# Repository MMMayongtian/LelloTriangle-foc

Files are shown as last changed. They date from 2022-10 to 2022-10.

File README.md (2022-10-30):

# 自平衡莱洛三角形可充电版

### 介绍
**在B站[“基于LQR控制器的自平衡莱洛三角形”](https://www.bilibili.com/video/BV19v411n7mN) 基础上添加了充电模块**
主控芯片使用ESP32，并配置了调参上位机，可以很方便的通过wifi无线调参。无刷控制使用灯哥开源FOC。制作出一个方便复刻的自平衡莱洛三角形，在桌面上作为一个摆件还是非常不错的
[展示视频](https://www.bilibili.com/video/BV1b3411x7za)

<center>V1(图一)</center>

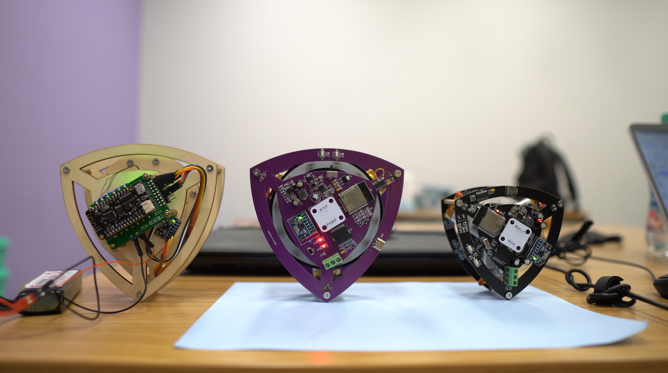
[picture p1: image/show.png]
V1


<center>V2(图二)</center>

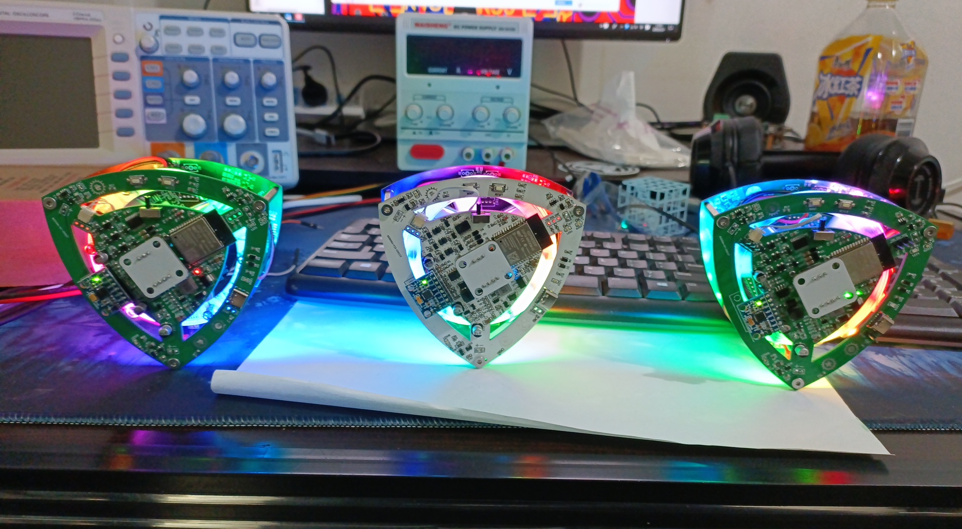
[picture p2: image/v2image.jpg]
V2


目前有两个版本
- V1(图1)：ESP32主控+L6234驱动+GB2204电机+CH340串口芯片+CS5095充电芯片
- V2(图2)：ESP32主控+EG2133+6mos驱动+2715电机+RGB+CM1010-A均衡芯片+CN3300充电芯片

**推荐制作V2，成功率高，效果更好，电机驱动芯片更便宜，还有RGB**

V1和V2**`电路图以及代码`**均在对应`V1\V2`文件夹(如需制作只要打开对应版本的文件夹即可，里面有对应的README说明)

### 1 软件架构
自平衡控制为LQR算法输出期望**速度**，使动量轮**加速运动**从而控制三角形左右方向。并且代码的调参都可以通过连接ESP32的wifi调整。具体特性如下：

- **基于 Arduino**：运行在 ESP32 Arduino 上
- **自带测试模式**：电压测试和速度测试，可以单独输出电压让电机转动，也可以设置指定速度让电机保持速度

Image text
### 2 硬件特性

| 说明 | 参数 |
| --- |--- |
| 莱洛三角形尺寸 | 100*100 mm  |
|动量轮尺寸|80*80 mm|
| 输入电压 | 3.7v锂电池*3|
|充电电压| 5V 从Type-C口输入|
| 主控芯片 | ESP-WROOM-32 |
|电机驱动|引脚:32, 33, 25|
|  AS5600 编码器 |SDA-23 SCL-5 　芯片要离径向磁铁有<font color='red'> 2mm以上高度 </font>|
| MPU6050六轴传感器  | SDA-19 SCL-18 |

### 3 硬件设计
使用立创EDA绘制电路原理图，LaserMaker绘制莱洛三角形和动量轮（有激光切割机可以事先切割结构作为参考）。将绘制完的图形导入到立创EDA中可作为PCB的外框。丝印图案分别是**Gawr Gura**、**ouro kronii** ~~helicopter~~

LaserMaker绘制的plt在**莱洛三角结构**文件夹内，需要重新绘制电路图可以使用

感谢嘉立创的PCB制板，使DIY电路制作变得非常便利，PCB制作开源点击

### 4 Ctrl+C +V（参考）
Arduino上的控制算法是原作者的LQR，无刷电机控制是灯哥开源FOC。电机控制引脚定义与传感器定义和灯哥开源FOC控制板2.0版一样。

EG2133无刷驱动为立创开源方案。

Python的GUI是以SimpleFOC的SimpleFOCStudio为基础，添加wifi功能。

V1的充电电路是立创广场开源的CS5095充电方案。

V2的充电电路是在立创广场开源的《CN3300 4串电池组板》方案基础上改的3串锂电池

PCB以及原理图技术支持——muyan

wifi效果以及按键面修复代码作者——muyan

1. 原作者：基于LQR控制器的自平衡莱洛三角形[BV19v411n7mN](https://www.bilibili.com/video/BV19v411n7mN)
2. muyan 立创链接[https://oshwhub.com/muyan2020?tab=project&page=1](https://oshwhub.com/muyan2020?tab=project&page=1)
3. muyan git链接[https://gitee.com/muyan3000](https://gitee.com/muyan3000)
4. EG2133驱动参考[https://oshwhub.com/acmetech-lceda/minifoc](https://oshwhub.com/acmetech-lceda/minifoc)
5. 灯哥开源FOC [https://gitee.com/ream_d/Deng-s-foc-controller](https://gitee.com/ream_d/Deng-s-foc-controller)
6. CS5095充电芯片电路[https://oshwhub.com/Aknice/cs5095e-san-jie-li-dian-chi-sheng-ya-chong-dian-dian-lu](https://oshwhub.com/Aknice/cs5095e-san-jie-li-dian-chi-sheng-ya-chong-dian-dian-lu)
7. CN3300 4串电池组板[https://oshwhub.com/583703056a/dian-chi-zu-ban_copy_copy](https://oshwhub.com/583703056a/dian-chi-zu-ban_copy_copy)
8. Arduino-Esp32环境提供者[https://github.com/kaliCYH](https://github.com/kaliCYH)

### 5 有用的地方

1. Arduino的程序中的command.h、command.cpp可以支持任意的字符串输入。在其他项目中一样可以用，无论是wifi接收到的字符串数据或者是串口的字符串数据。

2. GUI上位机可以在其他wifi项目中可以继续使用，用来调参还是很方便。

### 6 未解之谜

问题1：在传感器读取当前角度pitch在0和360来回切换时候，卡尔曼滤波值会慢慢变化，得到的值无法反映正确的当前角度。导致有一个面无法摇摆平衡。（已解决）（使用muyan的代码完美解决）

问题2：摇摆到平衡态时，参数不太好时，可能会摇摆过头，或者一直左右摇摆不能到平衡态。就算调好参数也会偶尔发生摇摆过头现象。（V2的2715电机可以让摇摆平衡的成功率提高到80%）

### 7 交流Q群

45coll电子交流QQ群：**824113552**

欢迎交流与沟通

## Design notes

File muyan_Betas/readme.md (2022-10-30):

# RGB自平衡莱洛三角形

#### 介绍

本版本是慕炎RGB版本程序 基于45°([https://gitee.com/coll45/foc/](https://gitee.com/coll45/foc/))程序修改

本版本虽然能在原版本pcb上运行，但完整功能需要对应的硬件支持才能获得

 **硬件要点** 

电机连接线线序按原插头顺序安装

动量轮的重量，建议安装所有孔位螺丝及螺母

磁铁的磁性为径向，而不是正反两面为NS

AS5600与磁铁的距离 0.3-3mm之内

可通过TTL观察simplefoc初始化时的状态提示判断，如果为PP Check：fail则需要检查磁铁及安装情况

【硬件基于45°工程文件修改的RGB版本】

[https://oshwhub.com/muyan2020/zi-ping-heng-di-lai-luo-san-jiao_10-10-ban-ben_copy](https://oshwhub.com/muyan2020/zi-ping-heng-di-lai-luo-san-jiao_10-10-ban-ben_copy)

1、去掉ch340和自动下载电路更换为rx tx插针，使用时不要连接3.3v插针，烧录前按住boot不放，再按一下reset，然后放掉所有键（如果打开串口监视发现数据乱码，把rx和tx线对换）

2、TPS54331更改为5V输出供电给RGB灯，5V输入到ams1117-3.3

3、预留2个触摸区和增加esp32状态灯，KEY3触摸开关灯，KEY4长按调光

4、无线充电功能（无线充电底座）

#### 软件架构

1、OTA

2、RGB灯控制程序

3、触摸控制程序

4、基于webserver的基础调参功能

#### webserver安装教程

webserver需要使用【ESP32 SPIFFS】文件上传

ESP32 SPIFFS文件上传方法

下载插件复制到C:\Program Files (x86)\Arduino\tools\ESP32FS\tool

重启Arduino即可

arduino-esp32fs-plugin

https://github.com/me-no-dev/arduino-esp32fs-plugin/releases/tag/1.0

使用时在arduino界面点“工具”-“ESP32 Sketch Data Upload”

#### 使用说明

Key3长按为开关RGB灯光

key4长按为增加亮度，放手后再次触摸为降低亮度

web页面调参

通过浏览器访问:[http://192.168.4.1](http://192.168.4.1)，用户名：admin 密码：reuleaux123(可通过修改代码修改)

#### 更新说明

### 20211229

1、增加OTA升级，第一次烧完固件后，再也不需要串口线了

2、增加webserver，通过手机浏览器访问192.168.4.1，直接可以进行数据查看和调参（调参功能还没做）

### 20220221

增加V2版本，电机是2715，对应极数7

V2版本的第三个按键，设定为wifi开关，按住2秒，ACT灯由亮转暗则设定完成

### 20220223

V1目录改为V1.5 为 GB2204 RGB版本

V1.5 V2修正摇摆无法平衡的问题

V2 默认不开启wifi，平衡后电流在50ma左右，开启wifi在100ma左右

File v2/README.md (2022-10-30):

# V2自平衡莱洛三角形可充电RGB版

### 介绍
该版本为2022/3/3制作的版本，无刷驱动使用EG2133可以成功使用esp32-arduino的simplefoc驱动。但是特殊情况下会mos管击穿冒烟，请使用带保护的锂电池，以防发生意外

`程序附件都在`gitee[https://gitee.com/coll45/foc]（https://gitee.com/coll45/foc）

V2
图片中间为立创smt版本，左为加热焊台一次焊成，右为使用热风枪分区域焊成。均可以摇摆平衡，使用2715电机

- mos管可以全部换成**AP2300**（更便宜一些），立创商城有售，测试过可以实现foc控制`（原理图用AO3400只是因为它是SMT基础库）`

- cn3300充电部分设计充电截至电压12.9V（考虑到电池内阻，最终充满电压为12.43V），充电电流0.5A，电感电流1.5A。充电功率为7.5W`（充电会电感部分会烫，但不至于烧毁电路）`

- 电机可以适配GB2204和2715无刷电机`(2715的平衡成功率高，因为KV值小)`

### 1 制作说明
[原理图以及PCB图链接](https://oshwhub.com/45coll/zi-ping-heng-di-lai-luo-san-jiao_10-10-ban-ben_copy)
1. 在立创开源链接中，点击`在编辑器中打开`，进入EDA页面，双击对应的PCB，上方导航栏找到-制造-PCB制板文件（gerber）-生成gerber-一键PCB/SMT下单。（一定要进编辑器！！！有遇到过开源链接的bom和真实bom对不上的情况）
2. 在下单页面中下单对应的pcb，如需SMT（机器贴片）可以选需要SMT，不选SMT会得到PCB空板（SMT到手之后需要焊30几个元器件，PCB空板为181个）
3. `淘宝购买`的表格是SMT和普通空板都要购买的
4. 普通空板，`BOM_莱洛三角V2`可以直接从立创商城**bom导入里面导入**
5. <font color='red'> 一定需要经向磁铁，物料清单里面已经给出，二选一</font>（磁环方便但是邮费贵，圆柱磁铁便宜包邮需要自行粘贴）
6. 焊接是基本功，最好是有风枪+烙铁的情况下尝试制作。

SMT注意：
- 选择需要SMT完成下单之后，进入订单界面。SMT分板定位孔选择-嘉立创添加，BOM与坐标清单选择-用我自己的BOM和坐标，导出文件选择-立创EDA。
- 需要上传的坐标文件和bom，都是在`EDA页面`-莱洛三角形PCB-制造-（物料清单BOM和坐标文件）中导出。
- 进入BOM匹配之后，左上角贴片数量选择-做5贴2（因为莱洛三角形制作一个需要两个PCB板，一个有元器件一个空板），贴片层-只贴顶层，产品类型-经济型，坐标文件生成方式-单板
- 强烈建议删除所有**扩展库以及推荐库**后打板`也可以删除AO3400这样可以便宜15元`（费用**做5贴2只需要90元**左右）
- SMT下单完成之后，只需购买`BOM_SMT购买专用_莱洛三角V2`，同样是从立创商城bom导入
- `BOM_SMT购买专用_莱洛三角V2`中给出的MOS管将AO3400替换成了AP2300

### 2 硬件特性

| 说明 | 参数 |
|---|---|
| 莱洛三角形尺寸 | 100*100 mm |
| 动量轮尺寸 | 80*80 mm |
| 电池*3 | 厚x长x宽:7.9mmx25mmx40mm 规格内均可 |
| 输入电压 | 3.7v锂电池*3 |
| 充电电压 | 5V 从Type-C口输入 |
| 充电芯片CN3300 | 5V输入,最大1.5A充电电流 |
| 均衡芯片CM1010-A | 电池电压超过4.25V之后开始放电 |
| 主控芯片 | ESP-WROOM-32 |
| 电机驱动芯片EG2133 | 引脚:32, 33, 25 |
| 稳压芯片TPS54331DR | 设置电池电压低于9V不工作，输出5.22V |
| AS5600 编码器 | SDA-23 SCL-5 　芯片要离磁铁有<font color='red'> 2mm以上高度 </font> |
| MPU6050六轴传感器 | SDA-19 SCL-18 |
| RGB灯-WS2812  | 使用GPIO16控制 |

| LED指示灯 | 功能 |
|---|---|
| LED1 | 串口指示灯，ESP32发送串口数据时会亮起 |
| LED2 | 充电完成指示灯，亮起表示充电完成，充到亮起可能需要2-3小时 |
| LED30 | 充电指示灯，亮起表示正在充电 |
| LED3 | typec的5V输入指示灯  接typec一定亮 |
| LED4 | 3.3v指示灯 电池输入12v输出3.3V |
| LED5 | 由GPIO4控制，电池电压低于9.5V时以1HZ频率闪烁 |
| LED27\28\29 | 均衡指示灯，亮起表示该电池电压高于4.25V正在通过22欧姆电阻放电中 |

| 触摸盘 | 功能 |
|---|---|
| 单击时长  | 100ms以上 |
| 长按时长  | 800ms以上 |
| 点赞触摸盘 | GPOI13-Touch4-单击:开关RGB灯；长按：开关wifi和电机  |
| 投币触摸盘 | GPOI15-Touch3-单击：增加RGB灯亮度；长按：下一个RGB灯效 |
| 收藏触摸盘 | GPOI2-Touch2-单击：减少RGB灯亮度；长按：上一个RGB灯效  |
### 3 使用说明

1. 下载完本git所有文件后，打开arduino文件夹，解压arduino.7z完成之后双击运行esp32_package_1.0.6.exe安装esp32库环境。注意：若之前有安装过arduino，请将路径`C:\Users\用户名\AppData\Local\`的Arduino15文件夹和`此电脑\文档`内的Arduino<font color='red'> 删除 </font>（~~也可自行下载Arduino并安装SimpleFOC~~）（但是可能会版本不对电机不动）
2. 打开解压后的arduino文件夹内的arduino.exe，导航栏-文件-打开。选择v2\main里面的main.ino
3. 使用CH340下载器，将下载器的TXD\RXD\GND用杜邦线引出，对准PCB的ESP32正上方的GND\RXD\TXD，接法为TXD-TXD\RXD-RXD\GND-GND
4. 将烧录程序到ESP32：选择工具-开发板-esp32 Arduino-ESP32 Dev module，然后连接USB口选择对应的com口，编译上传。
   1. 　<font color='red'> 如无法正常编译 </font>
      1. 可能与原有arduino冲突，请查看使用说明第一条
      2. 文件夹路径含有非法字符，可以把Arduino移动到硬盘根目录下，如D:\Arduino
5. 如需修改参数，长按点赞触摸盘，可以打开wifi并停止电机。
6. 打开本项目内的`python_gui`内的`可执行文件_main`内的**main.exe**并连接上WIFI：ESP32 。点击设置开始调参。
7. 连接成功后，点击disable，然后逆时针拨动动量轮，查看上位机中V参数是否为正值。注意！如果<font color='red'> 逆时针转为为负值 </font>那么需要将电机线任意两线互换。
Image text
8. 如果电机不能正常运行可以，点击上位机中最下方的<font color='red'> 测试部分 </font>，打开电压或者速度测试，滑动滑条，查看电机能否正常运行。如还不能请检测硬件电路部分。
9. 如果不能摇摆直立，推荐调整的参数为TA、SA、SV
10. K值可以用滑块调整，拖动滑块就会发送参数命令，但是调整到合适值之后需要自行在Arduino的main中修改再烧录一次

11. 滑条：最左边输入框为滑块下限，右边是滑块上限，滑条等分成**200**份，命令是**字符串**，滑动滑块发送**字符串** + **数值**

比如让平衡角度为90度，则输入：TA90，并且会存入eeprom的位置0中 注：wifi发送**命令不能过快**，因为每次都会保存进eeprom，K参数没有保存到EEPROM所以可以使用滑条调整。

| 参数命令 | 说明 |
| --- |--- |
| TA | target_angle平衡角度 例如TA89.3 设置平衡角度89.3| 
| SV | swing_up_voltage摇摆电压 左右摇摆的电压，越大越快到平衡态，但是过大会翻过头|
|SA|swing_up_angle摇摆角度 离平衡角度还有几度时候，切换到自平衡控制|
|VP1|速度环的PID的P，1是稳定在平衡角度之前的P值|
|VI1|速度环的PID的I，1是稳定在平衡角度之前的I值|
|VP2|速度环的PID的P，2是稳定后的P值|
|VI2|速度环的PID的I，2是稳定后的I值|
|K为LQR参数|**3和4**是速度控制稳定前和后|
|K3**1**|LQR的参数1：稳定前的角度差值|
|K3**2**|LQR的参数2：稳定前的左右倾倒加速度|
|K3**3**|LQR的参数3：稳定前的当前速度|
|K4**1**|LQR的参数1：稳定后的角度差值|
|K4**2**|LQR的参数2：稳定后的左右倾倒加速度|
|K4**3**|LQR的参数3：稳定后的当前速度|

LQR算法解释：当三角形向←倾斜时，需要产生向→的力回正。

在电压控制下：回正力F直接和输出电压值挂钩，向←倾斜，电机提供正电压V动量轮向**左加速转动**，产生向右的力F。

`期望电压 = 角度差值x参数1 + 左右倾倒加速度x参数2 + 当前速度x参数3`

在速度控制下：回正力F和动量轮转速加速度a有关，F = ma，向←倾斜，电机需要向**左加速转动**，产生向右的力F。

`期望速度 = 角度差值x参数1 + 左右倾倒加速度x参数2 + 当前速度x参数3`

两者区别：电压和速度控制都可以实现平衡，但因为使用simpleFOC控制电机转速无法无限加速，本电机实验最高转速180转，电压到上限12v。

使用电压控制会遇到，电机一下子就到了转速上限，就不能提供稳定的力F，参数调起来比较困难。

速度控制可以在偏差变大的时候，根据期望速度产生最大电压12v，并且不会超过电机最高转速。
### 4 硬件设计
使用立创EDA绘制电路原理图，LaserMaker绘制莱洛三角形和动量轮（有激光切割机可以事先切割结构作为参考）。将绘制完的图形导入到立创EDA中可作为PCB的外框。丝印图案分别是**Gawr Gura**、**ouro kronii** ~~helicopter~~

LaserMaker绘制的plt在**莱洛三角结构**文件夹内，需要重新绘制电路图可以使用

感谢嘉立创的PCB制板，使DIY电路制作变得非常便利，点击下方超链接可以前往嘉立创进行PCB制板

[莱洛三角形V2PCB](https://oshwhub.com/45coll/zi-ping-heng-di-lai-luo-san-jiao_10-10-ban-ben_copy)

### 5 Ctrl+C +V（参考）
Arduino上的控制算法是原作者的LQR，无刷驱动为立创开源的EG2133方案。

Python的GUI是以SimpleFOC的SimpleFOCStudio为基础，添加wifi功能。

V2的充电电路是在立创广场开源的《CN3300 4串电池组板》方案基础上改的3串锂电池

PCB以及原理图技术支持——muyan

wifi效果以及按键面修复代码作者——muyan

1. 原作者：基于LQR控制器的自平衡莱洛三角形[BV19v411n7mN](https://www.bilibili.com/video/BV19v411n7mN)
2. muyan立创链接[https://oshwhub.com/muyan2020?tab=project&page=1](https://oshwhub.com/muyan2020?tab=project&page=1)
3. muyan git链接[https://gitee.com/muyan3000](https://gitee.com/muyan3000)
4. EG2133驱动参考[https://oshwhub.com/acmetech-lceda/minifoc](https://oshwhub.com/acmetech-lceda/minifoc)
5. 灯哥开源FOC [https://gitee.com/ream_d/Deng-s-foc-controller](https://gitee.com/ream_d/Deng-s-foc-controller)
6. CN3300 4串电池组板[https://oshwhub.com/583703056a/dian-chi-zu-ban_copy_copy](https://oshwhub.com/583703056a/dian-chi-zu-ban_copy_copy)
7. Arduino环境提供者[https://github.com/kaliCYH](https://github.com/kaliCYH)

### 6 有用的地方

1. Arduino的程序中的command.h、command.cpp可以支持任意的字符串输入。在其他项目中一样可以用，无论是wifi接收到的字符串数据或者是串口的字符串数据。

2. GUI上位机可以在其他wifi项目中可以继续使用，用来调参还是很方便。

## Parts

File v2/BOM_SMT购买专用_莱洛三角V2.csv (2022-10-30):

ID | Name | Designator | Footprint | Quantity | Manufacturer Part | Manufacturer | Supplier | Supplier Part | Price
1 | M1010RS-03P | CN2 | CONN-SMD_M1010RS-03P | 1 | M1010RS-03P | XFCN(台湾兴飞) | LCSC | C541845 | 0.6462
2 | FR107_C2760867 | D4,D5,D6 | SOD-123FL_L2.7-W1.8-LS3.8-RD | 3 | FR107 | Slkor(萨科微) | LCSC | C2760867 | 0.067
3 | SMF5.0A_C908213 | D7 | SOD-123FL_L2.7-W1.8-LS3.8-RD | 1 | SMF5.0A | FUXINSEMI | LCSC | C908213 | 0.2007
4 | SJD12C6.5L01 | D8 | SOD-123_L2.8-W1.8-LS3.7-BI | 1 | SJD12C6.5L01 | Brightking Elec (TAIWAN) | LCSC | C313294 | 0.2679
5 | K2-3.6×6.1_SMD | KEY1,KEY2 | KEY-SMD_2P-L6.2-W3.6-LS8.0 | 2 | K2-1107ST-A4SW-06 |  | LCSC | C118141 | 0.4502
6 | 6.8uH | L1 | IND-SMD_L6.0-W6.0_SWPA6045S | 1 | SWPA6045S6R8MT | Sunlord | LCSC | C57254 | 0.5901
7 | 33uH | L2 | IND-SMD_L7.1-W6.6 | 1 | SLO0630H330MTT | Sunltech Tech | LCSC | C207844 | 0.737
8 | SK-12D02-VG5 | SW1 | SW-TH_SK-12D02-VG5 | 1 | SK-12D02-VG5 | Rectangular Connectors - Contacts | LCSC | C136722 | 0.5276
9 | CN3300 | U2 | SOT-23-6_L2.9-W1.6-P0.95-LS2.8-BL | 1 | CN3300 | CONSONANCE | LCSC | C52375 | 1.7574
10 | EG2133 | U7 | TSSOP-20_L6.5-W4.4-P0.65-LS6.4-BL | 1 | EG2133 | EG Micro | LCSC | C190343 | 1.95
11 | CM1010-A | U8,U9,U10 | SOT-23-6_L2.9-W1.6-P0.95-LS2.8-BR | 3 | CM1010-A | iCM(创芯微) | LCSC | C2685539 | 1.1691
12 | TYPE-603-T3 | USB1 | USB-C-SMD_TYPE-603-T3 | 1 | TYPE-603-T3 | Yuandi(台湾元迪) | LCSC | C2689837 | 0.505
13 | 47uF | C4,C7,C17 | CAP-SMD_BD5.0-L5.3-W5.3-RD | 3 | CS1C470M-CRD54 | SEMTECH | LCSC | C96178 | 0.1769
14 | AP2300 | Q1,Q3,Q4,Q5,Q6,Q7,Q8,Q9,Q10,Q11 | SOT-23-3_L2.9-W1.6-P1.90-LS2.8-BR | 10 | AP2300 | ALLPOWER(铨力) | LCSC | C360338 | 0.163056

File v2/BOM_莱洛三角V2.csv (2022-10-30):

ID | Name | Designator | Footprint | Quantity | Manufacturer Part | Manufacturer | Supplier | Supplier Part | Price
1 | 22UF | C1,C14 | C0805 | 2 | CL31A226KPHNNNE | SAMSUNG | LCSC | C5672 | 0.2392
2 | 100nF | C2,C5,C6,C13,C16,C21,C22,C23,C24,C25,C26,C27,C28,C29,C30,C31,C32,C33,C34,C35,C36,C37,C38,C39,C40,C41,C42,C46,C47,C48 | C0603 | 30 | CC0603KRX7R9BB104 | YAGEO | LCSC | C14663 | 0.0154
3 | 1uF | C3,C15,C44 | C0603 | 3 | CL10A105KB8NNNC | SAMSUNG | LCSC | C15849 | 0.0331
4 | 47uF | C4,C7,C17 | CAP-SMD_BD5.0-L5.3-W5.3-RD | 3 | CS1C470M-CRD54 | SEMTECH | LCSC | C96178 | 0.1757
5 | 10nF | C8,C11,C12 | C0603 | 3 | 0603B103K500NT | FH | LCSC | C57112 | 0.0155
6 | 1nF | C9 | C0603 | 1 | CL10B102KB8NNNC | SAMSUNG | LCSC | C1588 | 0.0162
7 | 47pF | C10 | C0603 | 1 | CL10C470JB8NNNC | SAMSUNG | LCSC | C1671 | 0.0314
8 | 4.7uF | C43 | C0603 | 1 | CL10A475KO8NNNC | SAMSUNG | LCSC | C19666 | 0.0657
9 | 22pF | C45 | C0603 | 1 | CL10C220JB8NNNC | SAMSUNG | LCSC | C1653 | 0.0321
10 | M1010RS-03P | CN2 | CONN-SMD_M1010RS-03P | 1 | M1010RS-03P | XFCN(台湾兴飞) | LCSC | C541845 | 0.6462
11 | SS34_C8678 | D1,D3 | DO-214AC_L4.3-W2.7-LS5.3-RD | 2 | SS34 | MDD | LCSC | C8678 | 0.2931
12 | ZMM3V3 | D2 | LL-34_L3.5-W1.5-RD | 1 | ZMM3V3 | SEMTECH | LCSC | C8056 | 0.13
13 | FR107_C2760867 | D4,D5,D6 | SOD-123FL_L2.7-W1.8-LS3.8-RD | 3 | FR107 | Slkor(萨科微) | LCSC | C2760867 | 0.067
14 | SMF5.0A_C908213 | D7 | SOD-123FL_L2.7-W1.8-LS3.8-RD | 1 | SMF5.0A | FUXINSEMI | LCSC | C908213 | 0.2007
15 | SJD12C6.5L01 | D8 | SOD-123_L2.8-W1.8-LS3.7-BI | 1 | SJD12C6.5L01 | Brightking Elec (TAIWAN) | LCSC | C313294 | 0.2679
16 | 1N4148W_C81598 | D9,D10,D11,D12,D13,D14 | SOD-123F_L2.7-W1.6-LS3.8-RD | 6 | 1N4148W | SEMTECH | LCSC | C81598 | 0.0761
17 | K2-3.6×6.1_SMD | KEY1,KEY2 | KEY-SMD_2P-L6.2-W3.6-LS8.0 | 2 | K2-1107ST-A4SW-06 |  | LCSC | C118141 | 0.4502
18 | 6.8uH | L1 | IND-SMD_L6.0-W6.0_SWPA6045S | 1 | SWPA6045S6R8MT | Sunlord | LCSC | C57254 | 0.5901
19 | 33uH | L2 | IND-SMD_L7.1-W6.6 | 1 | SLO0630H330MTT | Sunltech Tech | LCSC | C207844 | 0.737
20 | 19-217/BHC-ZL1M2RY/3T | LED1,LED2,LED3,LED4,LED5,LED27,LED28,LED29 | LED0603-R-RD | 8 | 19-217/BHC-ZL1M2RY/3T | EVERLIGHT | LCSC | C72041 | 0.1116
21 | AP2300 | Q1,Q3,Q4,Q5,Q6,Q7,Q8,Q9,Q10,Q11 | SOT-23-3_L2.9-W1.6-P1.90-LS2.8-BR | 10 | AP2300 | ALLPOWER(铨力) | LCSC | C360338 | 0.163056
22 | S8050_C2146 | Q2,Q12 | SOT-23-3_L3.0-W1.7-P0.95-LS2.9-BR | 2 | S8050 | CJ | LCSC | C2146 | 0.129
23 | 120 | R1,R2 | R0603 | 2 | 0603WAF1200T5E | UniOhm | LCSC | C22787 | 0.0081
24 | 62K | R3,R5 | R0603 | 2 | 0603WAF6202T5E | UniOhm | LCSC | C23221 | 0.0074
25 | 56K | R4 | R0603 | 1 | 0603WAF5602T5E | UniOhm | LCSC | C23206 | 0.0077
26 | 10K | R6,R7,R9,R10,R11,R14,R15,R20,R21,R22,R23,R24,R30,R31,R32,R33,R40,R41,R47,R48,R49 | R0603 | 21 | 0603WAF1002T5E | UniOhm | LCSC | C25804 | 0.0073
27 | 27K | R8 | R0603 | 1 | 0603WAF2702T5E | UniOhm | LCSC | C22967 | 0.0077
28 | 1K | R12,R26,R28,R29 | R0603 | 4 | 0603WAF1001T5E | UniOhm | LCSC | C21190 | 0.0064
29 | 4.7K | R13,R34,R35 | R0603 | 3 | 0603WAF4701T5E | UniOhm | LCSC | C23162 | 0.0081
30 | 0.1 | R16 | R1206 | 1 | 1206W4F100LT5E | UniOhm | LCSC | C25334 | 0.0573
31 | 470 | R17,R18,R19 | R0603 | 3 | 0603WAF4700T5E | UniOhm | LCSC | C23179 | 0.0074
32 | 22Ω | R25,R27,R50 | R1206 | 3 | 1206W4F220JT5E | UniOhm | LCSC | C17958 | 0.0258
33 | 10Ω | R36,R42,R43,R44,R45,R46 | R0603 | 6 | 0603WAF100JT5E | UniOhm | LCSC | C22859 | 0.0078
34 | 300 | R37,R51 | R0603 | 2 | 0603WAF3000T5E | UniOhm | LCSC | C23025 | 0.0073
35 | 1.2K | R38 | R0603 | 1 | 0603WAF1201T5E | UniOhm | LCSC | C22765 | 0.0077
36 | 11K | R39 | R0603 | 1 | 0603WAF1102T5E | UniOhm | LCSC | C25950 | 0.0098
37 | SK-12D02-VG5 | SW1 | SW-TH_SK-12D02-VG5 | 1 | SK-12D02-VG5 | Rectangular Connectors - Contacts | LCSC | C136722 | 0.5276
38 | TPS54331DR | U1 | SOIC-8_L5.0-W4.0-P1.27-LS6.0-BL-EP | 1 | TPS54331DR | TI | LCSC | C9865 | 2.3
39 | CN3300 | U2 | SOT-23-6_L2.9-W1.6-P0.95-LS2.8-BL | 1 | CN3300 | CONSONANCE | LCSC | C52375 | 1.7574
40 | AMS1117-3.3 | U5 | SOT-223-3_L6.5-W3.4-P2.30-LS7.0-BR | 1 | AMS1117-3.3 | AMS | LCSC | C6186 | 0.9989
41 | EG2133 | U7 | TSSOP-20_L6.5-W4.4-P0.65-LS6.4-BL | 1 | EG2133 | EG Micro | LCSC | C190343 | 1.95
42 | CM1010-A | U8,U9,U10 | SOT-23-6_L2.9-W1.6-P0.95-LS2.8-BR | 3 | CM1010-A | iCM(创芯微) | LCSC | C2685539 | 1.1691
43 | TYPE-603-T3 | USB1 | USB-C-SMD_TYPE-603-T3 | 1 | TYPE-603-T3 | Yuandi(台湾元迪) | LCSC | C2689837 | 0.505
44 | 22uF | C18,C19,C20 | C0603 | 3 | CL10A226MQ8NRNC | SAMSUNG | LCSC | C59461 | 0.056

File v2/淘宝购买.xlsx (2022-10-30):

商品名称 | 数量 | 价格 | 淘宝链接
ESP-WROOM-32 选ESP-WROOM-32模组 | 1 | 11.5 | https://item.taobao.com/item.htm?spm=a1z10.3-c-s.w4002-23633313809.19.3dfb546e6TpzCy&id=551532642694
MPU-6050模块 | 1 | 5.6 | https://item.taobao.com/item.htm?spm=a1z09.2.0.0.13962e8dMoPn2X&id=16630417522&_u=q1sddf3scdf9
AS5600磁编码器 | 1 | 7.3 | https://item.taobao.com/item.htm?spm=a1z09.2.0.0.13962e8dMoPn2X&id=622544987536&_u=q1sddf3sa81a
ch340G USB转TTL 下载器 | 1 | 3.05 | https://item.taobao.com/item.htm?spm=a1z10.3-c-s.w4002-23633313809.9.671f546eIWPZyu&id=17817178269
40脚2.54mm单排针 （颜色随意） | 1 | 0.1 | https://item.taobao.com/item.htm?spm=a1z10.3-c-s.w4002-23633313809.10.c412546e6Qs8yh&id=14591564405
2.54MM间距单排母 3P一个 4P一个（也可以买40P的自己剪） | 1 | 0.15 | https://item.taobao.com/item.htm?spm=a1z10.3-c-s.w4002-23633313809.13.6571546eNITJtV&id=15813904618
2.54MM 40P杜邦线 公对母 | 1 | 1.75 | https://item.taobao.com/item.htm?spm=a1z10.3-c-s.w4002-23633313809.11.5880546eZ9Ny5b&id=16412228723
电机可选型号为GB2204和2715无刷电机（强烈推荐2715平衡性能好）
GB2204无刷电机 | 1 | 4.8 | https://item.taobao.com/item.htm?spm=a1z10.3-c-s.w4002-5028031793.9.33327160LLxtbT&id=596506316013
钕铁硼高强磁 直流无刷电机 2715 航模云台电机 | 1 | 7.6 | https://item.taobao.com/item.htm?id=597027494849&ns=1&abbucket=17 (https://item.taobao.com/item.htm?spm=a230r.1.14.1.4b561ff98WXXd3&id=597027494849&ns=1&abbucket=17)
以下磁铁二选一购买
径向磁铁 6*3mm | 10 | 9.9 | https://item.taobao.com/item.htm?spm=a1z0d.6639537.1997196601.4.beda7484epF01m&id=596454786426
径向磁环 D6*D3*4 | 1 | 1.92 | https://item.taobao.com/item.htm?spm=a1z0d.6639537.1997196601.4.2e0e7484hGRPi2&id=656463127193
锂电池3.7v 602535 600毫安 （正负线可以直接焊PCB上） | 3 | 5 | https://item.taobao.com/item.htm?spm=a1z09.2.0.0.75532e8dnYo6W1&id=551668511973&_u=f1sddf3sea89
以下紧固件只需要拍一件（数量做一套所需的数量）
35mm-M3铜柱 使用3个 | 1 | 3 | https://detail.tmall.com/item.htm?id=17318980620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
M3六角螺帽 使用3个 | 1 | 1.64 | https://detail.tmall.com/item.htm?id=20955552239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
M3*6平头螺丝 使用3个 | 1 | 3.08 | https://detail.tmall.com/item.htm?id=15817242523&skuId=4912759730383
M1.6*4十字圆头螺丝螺 使用8个 | 1 | 2.42 | https://detail.tmall.com/item.htm?id=18236357036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
M5*8六角螺丝螺栓螺母套装 使用12个（螺丝+螺母+垫片） | 1 | 5.8 | https://detail.tmall.com/item.htm?id=593829755002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
WS2812B 5050RGB幻彩四脚内置驱动IC灯珠5V | 21 | 0.14 | https://item.taobao.com/item.htm?id=626235317413&ns=1&abbucket=17 (https://item.taobao.com/item.htm?spm=a230r.1.14.119.58de714ed7XBaN&id=626235317413&ns=1&abbucket=17)

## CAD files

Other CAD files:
莱洛三角结构/V2动量轮图案.dxf
莱洛三角结构/V2-M5孔动量轮8cm.dxf
莱洛三角结构/V1莱洛三角形10cm.dxf
莱洛三角结构/V1动量轮8cm.dxf

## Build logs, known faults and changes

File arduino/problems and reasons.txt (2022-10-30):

问题1：wifi接受到的数据为const uint_8  不能直接用atoi转换为int。
解决：atoi((char*)(packet.data())) //使用(char*) 进行强制类型转换

问题2：c语言中sizeof()返回的是变量声明后所占的内存数，不是实际长度。strlen是一个函数，求的是字符串的实际长度，它求得方法是从开始到遇到第一个'\0',如果你只定义没有给它赋初值，这个结果是不定的，它会从arr首地址一直找下去，直到遇到'\0'停止
解决：字符串转换中使用strlen()获得实际长度

问题3：数字转字符串中可以使用sprintf
解决：sprintf(s, "%d", 100//将100转为10进制表示的字符串

问题4：强制类型转换(const unsigned char*)不能直接使用print输出
解决：atoi((char*)(packet.data())) //使用(char*) 进行强制类型转换

问题5: udp发送数据时会出现乱码
解决：字符数组末尾需要添加'\0'作为结束符

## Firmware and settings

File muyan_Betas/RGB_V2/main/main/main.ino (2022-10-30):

/**
   自平衡莱洛三角形 RGB版  HW:Ver 2.0  FW:Ver 1.2.1
   立创EDA https://oshwhub.com/muyan2020/zi-ping-heng-di-lai-luo-san-jiao_10-10-ban-ben_copy
   RGB版本程序 https://gitee.com/muyan3000/RGBFOC 基于45°(https://gitee.com/coll45/foc/)程序修改
   arduino开发环境-灯哥开源FOChttps://gitee.com/ream_d/Deng-s-foc-controller，并安装Kalman。

  FOC引脚32, 33, 25, 22    22为enable
  AS5600霍尔传感器 SDA-23 SCL-5  MPU6050六轴传感器 SDA-19 SCL-18
  本程序有两种平衡方式， FLAG_V为1时使用电压控制，为0时候速度控制。电压控制时LQR参数使用K1和K2，速度控制时LQR参数使用K3和K4
  在wifi上位机窗口中输入：TA+角度，就可以修改平衡角度
  比如让平衡角度为90度，则输入：TA90，并且会存入eeprom的位置0中 注：wifi发送命令不能过快，因为每次都会保存进eeprom
  在使用自己的电机时，请一定记得修改默认极对数，即 BLDCMotor(5) 中的值，设置为自己的极对数数字，磁铁数量/2
  程序默认设置的供电电压为 12V,用其他电压供电请记得修改 voltage_power_supply , voltage_limit 变量中的值
  V1默认PID针对的电机是 GB2204 ，使用自己的电机需要修改PID参数，才能实现更好效果
  V2电机是2715
*/
#include <SimpleFOC.h>
#include "Command.h"
#include <WiFi.h>
#include <AsyncUDP.h> //引用以使用异步UDP
#include "Kalman.h" // Source: https://github.com/TKJElectronics/KalmanFilter
#include "EEPROM.h"

#include <ESPmDNS.h>
#include <ArduinoOTA.h>
#include <WebServer.h>
#include <FS.h>
#include "SPIFFS.h"
#include <time.h>
#define timezone 8

#include <FastLED.h>
#define DATA_PIN    16    //RGB pin
#define LED_TYPE    WS2812B
#define COLOR_ORDER GRB
#define NUM_LEDS    21  //LED数量
int rgb_brightness = 25;  //初始化亮度
CRGB leds[NUM_LEDS];

unsigned long TenthSecondsSinceStart = 0;
void TenthSecondsSinceStartTask();
void OnTenthSecond();
void OnSecond();
void StartWebServer();

#define ACTIVE_PIN 4  //状态灯
#define BAT_VOLTAGE_SENSE_PIN 34  //电池电压检测ADC，如果旧版PCB无电压检测电路，则注释掉此行
const double R1_VOLTAGE = 68000; //68K
const double R2_VOLTAGE = 10000; //10K
const double min_voltage  = 9.5;  //电池检测最低电压
double bat_voltage;

const int threshold_top = 20;   //触摸顶部阈值
const int threshold_bottom = 1;   //触摸底部阈值，越接近数值越小
const int threshold_count = 4;   //触摸计数器有效值，通常会有意外的自动触发

int touchread[4] = {100, 100, 100, 100}; //初始化触摸读取值为100，无触摸
int touchDetected[4] = {}; //通过touchdetected持续计数判断是否按键，防止无触碰触发

bool touch_touched[4] = {};   //单击判断
int touch_touched_times[4] = {};  //单击次数，单击切换模式，双击
int touch_touching_time[4] = {}; //持续触摸秒数，用于判断长按事件，长按关闭，长按开启，开启状态长按调光，
bool touch_STATE[4] = {1, 1, 1, 0}; // 定义按键触发对象状态变量初始值为true默认开启 T2 T3 T4

const char *username = "admin";     //web用户名
const char *userpassword = "reuleaux123"; //web用户密码
const char *ServerName = "ESP32-Reuleaux-RGB";
char mac_tmp[6];
const char *ssid = mac_tmp;
const char *password = "Reul12345678";
char DateTimeStr[20]  = "1970-01-01 00:00:00";
char Debug_Log[255][255];
uint32_t loop_time_begin = millis();
int debug_times;
bool log_control = 0, debug_log_control = 0;

WebServer ESP32Server(80);

Kalman kalmanZ;
#define gyroZ_OFF -0.19
/* ----IMU Data---- */

double accX, accY, accZ;
double gyroX, gyroY, gyroZ;
int16_t tempRaw;
bool stable = 0 , battery_low = 0;
uint32_t last_unstable_time;
uint32_t last_stable_time;

double gyroZangle; // Angle calculate using the gyro only
double compAngleZ; // Calculated angle using a complementary filter
double kalAngleZ;  // Calculated angle using a Kalman filter
float pendulum_angle;

uint32_t timer;
uint8_t i2cData[14]; // Buffer for I2C data
/* ----FOC Data---- */

// driver instance
double acc2rotation(double x, double y);
float constrainAngle(float x);

bool wifi_flag = 0;
AsyncUDP udp;                     //创建UDP对象
unsigned int localUdpPort = 2333; //本地端口号
void wifi_print(char * s, double num);

MagneticSensorI2C sensor = MagneticSensorI2C(AS5600_I2C);
TwoWire I2Ctwo = TwoWire(1);
LowPassFilter lpf_throttle{0.00};

//倒立摇摆参数
//3和4是速度控制稳定前和后
float LQR_K3_1 = 10;   //速度控制摇摆到平衡
float LQR_K3_2 = 1.7;   //
float LQR_K3_3 = 1.75; //

float LQR_K4_1 = 2.4;   //速度控制平衡态
float LQR_K4_2 = 1.5;   //
float LQR_K4_3 = 1.42; //

//电机参数
BLDCMotor motor = BLDCMotor(7); //电机极数
BLDCDriver3PWM driver = BLDCDriver3PWM(32, 33, 25, 22);
float target_velocity = 0;	//目标速度
float target_angle = 89.3;	//平衡角度 例如TA89.3 设置平衡角度89.3
float target_voltage = 0;	//目标电压
float swing_up_voltage = 1.8;	//摇摆电压 左右摇摆的电压，越大越快到平衡态，但是过大会翻过头
float swing_up_angle = 20;	//摇摆角度 离平衡角度还有几度时候，切换到自平衡控制
float v_i_1 = 20;	//非稳态速度环I
float v_p_1 = 0.5;	//非稳态速度环P
float v_i_2 = 10;	//稳态速度环I
float v_p_2 = 0.2;	//稳态速度环P
//命令设置
Command comm;
bool Motor_enable_flag = 0;
int test_flag = 0;
void do_TA(char* cmd) {
  comm.scalar(&target_angle, cmd);
  EEPROM.writeFloat(0, target_angle);
}
void do_SV(char* cmd) {
  comm.scalar(&swing_up_voltage, cmd);
  EEPROM.writeFloat(4, swing_up_voltage);
}
void do_SA(char* cmd) {
  comm.scalar(&swing_up_angle, cmd);
  EEPROM.writeFloat(8, swing_up_angle);
}

void do_START(char* cmd) {
  wifi_flag = !wifi_flag;
}
void do_MOTOR(char* cmd)
{
  if (Motor_enable_flag)
    motor.enable();
  else
    motor.disable();
  Motor_enable_flag = !Motor_enable_flag;
}

void do_TVQ(char* cmd)
{
  if (test_flag == 1)
    test_flag = 0;
  else
    test_flag = 1;
}
void do_TVV(char* cmd)
{
  if (test_flag == 2)
    test_flag = 0;
  else
    test_flag = 2;
}
void do_VV(char* cmd) {
  comm.scalar(&target_velocity, cmd);
}
void do_VQ(char* cmd) {
  comm.scalar(&target_voltage, cmd);
}

void do_vp1(char* cmd) {
  comm.scalar(&v_p_1, cmd);
  EEPROM.writeFloat(12, v_p_1);
}
void do_vi1(char* cmd) {
  comm.scalar(&v_i_1, cmd);
  EEPROM.writeFloat(16, v_i_1);
}
void do_vp2(char* cmd) {
  comm.scalar(&v_p_2, cmd);
  EEPROM.writeFloat(20, v_p_2);
}
void do_vi2(char* cmd) {
  comm.scalar(&v_i_2, cmd);
  EEPROM.writeFloat(24, v_i_2);
}
void do_tv(char* cmd) {
  comm.scalar(&target_velocity, cmd);
}
void do_K31(char* cmd) {
  comm.scalar(&LQR_K3_1, cmd);
}
void do_K32(char* cmd) {
  comm.scalar(&LQR_K3_2, cmd);
}
void do_K33(char* cmd) {
  comm.scalar(&LQR_K3_3, cmd);
}
void do_K41(char* cmd) {
  comm.scalar(&LQR_K4_1, cmd);
}
void do_K42(char* cmd) {
  comm.scalar(&LQR_K4_2, cmd);
}
void do_K43(char* cmd) {
  comm.scalar(&LQR_K4_3, cmd);
}

void Debug_Log_func(String debuglog, bool debug_control = debug_log_control) {
  if (debug_control) {
    uint32_t tmp_loop_time_begin = millis();
    sprintf(Debug_Log[debug_times], "%s\r\nBegin time:%d\tEnd time:%d\tProcessed in %d ms\tFreeHeap:%d\r\n%s", Debug_Log[debug_times], loop_time_begin, tmp_loop_time_begin, (tmp_loop_time_begin - loop_time_begin), ESP.getFreeHeap(), debuglog.c_str());
    loop_time_begin = tmp_loop_time_begin;
    debug_times++;
  }
}

bool AutoWifiConfig()
{
  //wifi初始化
  WiFi.mode(WIFI_AP);
  while (!WiFi.softAP(ssid, password)) {}; //启动AP
  Serial.println("AP启动成功");
  Serial.println("Ready");
  Serial.print("IP address: ");
  Serial.println(WiFi.softAPIP());
  byte mac[6];
  WiFi.macAddress(mac);
  WiFi.setHostname(ServerName);
  Serial.printf("macAddress 0x%02X:0x%02X:0x%02X:0x%02X:0x%02X:0x%02X\r\n", mac[0], mac[1], mac[2], mac[3], mac[4], mac[5]);
  
  while (!udp.listen(localUdpPort)) //等待udp监听设置成功
  {
  }
  udp.onPacket(onPacketCallBack); //注册收到数据包事件

  ArduinoOTA.setHostname(ServerName);
  //以下是启动OTA，可以通过WiFi刷新固件
  ArduinoOTA.onStart([]() {
    String type;
    if (ArduinoOTA.getCommand() == U_FLASH) {
      type = "sketch";
    } else { // U_SPIFFS
      type = "filesystem";
    }

    // NOTE: if updating SPIFFS this would be the place to unmount SPIFFS using SPIFFS.end()
    Serial.println("Start updating " + type);
  });
  ArduinoOTA.onEnd([]() {
    Serial.println("\nEnd");
  });
  ArduinoOTA.onProgress([](unsigned int progress, unsigned int total) {
    Serial.printf("Progress: %u%%\r", (progress / (total / 100)));
  });
  ArduinoOTA.onError([](ota_error_t error) {
    Serial.printf("Error[%u]: ", error);
    if (error == OTA_AUTH_ERROR) {
      Serial.println("Auth Failed");
    } else if (error == OTA_BEGIN_ERROR) {
      Serial.println("Begin Failed");
    } else if (error == OTA_CONNECT_ERROR) {
      Serial.println("Connect Failed");
    } else if (error == OTA_RECEIVE_ERROR) {
      Serial.println("Receive Failed");
    } else if (error == OTA_END_ERROR) {
      Serial.println("End Failed");
    }
  });
  ArduinoOTA.begin();
}

void onPacketCallBack(AsyncUDPPacket packet)
{
  char* da;
  da = (char*)(packet.data());
  Serial.println(da);
  comm.run(da);
  EEPROM.commit();
  //  packet.print("reply data");
}
// instantiate the commander
void setup() {
  Debug_Log_func("Before setup", 1);
  Serial.begin(115200);

  pinMode(ACTIVE_PIN, OUTPUT);
  digitalWrite(ACTIVE_PIN, HIGH);

  uint32_t chipId = 0;
  for (int i = 0; i < 17; i = i + 8) {
    chipId |= ((ESP.getEfuseMac() >> (40 - i)) & 0xff) << i;
  }
  Serial.printf("Chip ID: %d\r\n", chipId);

  Serial.printf("ESP32 Chip ID = %04X", (uint16_t)(ESP.getEfuseMac() >> 32)); //print High 2 bytes
  Serial.printf("%08X\r\n", (uint32_t)ESP.getEfuseMac()); //print Low 4bytes.

  Serial.printf("Chip model = %s Rev %d\r\n", ESP.getChipModel(), ESP.getChipRevision());
  Serial.printf("This chip has %d cores CpuFreqMHz = %u\r\n", ESP.getChipCores(), ESP.getCpuFreqMHz());
  Serial.printf("get Cycle Count = %u\r\n", ESP.getCycleCount());
  Serial.printf("SDK version:%s\r\n", ESP.getSdkVersion());  //获取IDF版本

  //获取片内内存	Internal RAM
  Serial.printf("Total heap size = %u\t", ESP.getHeapSize());
  Serial.printf("Available heap = %u\r\n", ESP.getFreeHeap());
  Serial.printf("Lowest level of free heap since boot = %u\r\n", ESP.getMinFreeHeap());
  Serial.printf("Largest block of heap that can be allocated at once = %u\r\n", ESP.getMaxAllocHeap());

  //SPI RAM
  Serial.printf("Total Psram size = %u\t", ESP.getPsramSize());
  Serial.printf("Available Psram = %u\r\n", ESP.getFreePsram());
  Serial.printf("Lowest level of free Psram since boot = %u\r\n", ESP.getMinFreePsram());
  Serial.printf("Largest block of Psram that can be allocated at once = %u\r\n", ESP.getMinFreePsram());

  if (!EEPROM.begin(1000)) {
    Serial.println("Failed to initialise EEPROM");
    Serial.println("Restarting...");
    delay(1000);
    esp_restart();
  }
  // eeprom 读取
  int k, j;
  j = 0;
  for (k = 0; k <= 24; k = k + 4)
  {
    float nan = EEPROM.readFloat(k);
    if (isnan(nan))
    {
      j = 1;
      Serial.println("frist write");
      EEPROM.writeFloat(0, target_angle);       delay(10); EEPROM.commit();
      EEPROM.writeFloat(4, swing_up_voltage);      delay(10); EEPROM.commit();
      EEPROM.writeFloat(8, swing_up_angle);      delay(10); EEPROM.commit();
      EEPROM.writeFloat(12, v_p_1);      delay(10); EEPROM.commit();
      EEPROM.writeFloat(16, v_i_1);      delay(10); EEPROM.commit();
      EEPROM.writeFloat(20, v_p_2);      delay(10); EEPROM.commit();
      EEPROM.writeFloat(24, v_i_2);       delay(10); EEPROM.commit();
    }
  }
  if (j == 0)
  {
    target_angle = EEPROM.readFloat(0);
    swing_up_voltage = EEPROM.readFloat(4);
    swing_up_angle = EEPROM.readFloat(8);
    v_p_1 = EEPROM.readFloat(12);
    v_i_1 = EEPROM.readFloat(16);
    v_p_2 = EEPROM.readFloat(20);
    v_i_2 = EEPROM.readFloat(24);
    motor.PID_velocity.P = v_p_1;
    motor.PID_velocity.I = v_i_1;
  }

  //命令设置
  comm.add("TA", do_TA);
  comm.add("START", do_START);
  comm.add("MOTOR", do_MOTOR);
  comm.add("SV", do_SV);
  comm.add("SA", do_SA);
  comm.add("TVQ", do_TVQ);
  comm.add("TVV", do_TVV);
  comm.add("VV", do_VV);
  comm.add("VQ", do_VQ);
  //速度环参数
  comm.add("VP1", do_vp1);
  comm.add("VI1", do_vi1);
  comm.add("VP2", do_vp2);
  comm.add("VI2", do_vi2);
  comm.add("TV", do_tv);
  comm.add("K31", do_K31);
  comm.add("K32", do_K32);
  comm.add("K33", do_K33);
  comm.add("K41", do_K41);
  comm.add("K42", do_K42);
  comm.add("K43", do_K43);

  // tell FastLED about the LED strip configuration
  FastLED.addLeds<LED_TYPE, DATA_PIN, COLOR_ORDER>(leds, NUM_LEDS)
  .setCorrection(TypicalLEDStrip)
  .setDither(rgb_brightness < 255);
  // set master brightness control
  FastLED.setBrightness(rgb_brightness);

  CRGB c_rgb[5];
  c_rgb[0]  = CRGB::White;
  c_rgb[2]  = CRGB::Red;
  c_rgb[1]  = CRGB::Green;
  c_rgb[3]  = CRGB::Blue;
  c_rgb[4]  = CRGB::Purple;

  for ( int j = 0; j < 5; j++) {
    for ( int i = 0; i < NUM_LEDS; i++) {
      leds[i] = c_rgb[j];
      FastLED.show();
      delay(15);
    }
    delay(300);
  }

  sprintf(mac_tmp, "%02X\r\n", (uint32_t)(ESP.getEfuseMac() >> (24) ));
  sprintf(mac_tmp, "ESP32-%c%c%c%c%c%c", mac_tmp[4], mac_tmp[5], mac_tmp[2], mac_tmp[3], mac_tmp[0], mac_tmp[1] );

  if ( touch_STATE[3] ) {
    AutoWifiConfig();
    StartWebServer();
  }


  // kalman mpu6050 init
  Wire.begin(19, 18, 400000); // Set I2C frequency to 400kHz
  i2cData[0] = 7;    // Set the sample rate to 1000Hz - 8kHz/(7+1) = 1000Hz
  i2cData[1] = 0x00; // Disable FSYNC and set 260 Hz Acc filtering, 256 Hz Gyro filtering, 8 KHz sampling
  i2cData[2] = 0x00; // Set Gyro Full Scale Range to ±250deg/s
  i2cData[3] = 0x00; // Set Accelerometer Full Scale Range to ±2g
  while (i2cWrite(0x19, i2cData, 4, false)); // Write to all four registers at once
  while (i2cWrite(0x6B, 0x01, true)); // PLL with X axis gyroscope reference and disable sleep mode
  while (i2cRead(0x75, i2cData, 1));
  if (i2cData[0] != 0x68)
  { // Read "WHO_AM_I" register
    Serial.print(F("Error reading sensor"));
    while (1);
  }

  delay(100); // Wait for sensor to stabilize

  /* Set kalman and gyro starting angle */
  while (i2cRead(0x3B, i2cData, 6));
  accX = (int16_t)((i2cData[0] << 8) | i2cData[1]);
  accY = (int16_t)((i2cData[2] << 8) | i2cData[3]);
  accZ = (int16_t)((i2cData[4] << 8) | i2cData[5]);
  double pitch = acc2rotation(accX, accY);
  kalmanZ.setAngle(pitch); // Set starting angle
  gyroZangle = pitch;
  timer = micros();
  Serial.println("kalman mpu6050 init");

  I2Ctwo.begin(23, 5, 400000);   //SDA,SCL
  sensor.init(&I2Ctwo);

  //连接motor对象与传感器对象
  motor.linkSensor(&sensor);

  //供电电压设置 [V]
  driver.voltage_power_supply = 12;
  driver.init();

  //连接电机和driver对象
  motor.linkDriver(&driver);

  //FOC模型选择
  motor.foc_modulation = FOCModulationType::SpaceVectorPWM;

  //运动控制模式设置
  motor.controller = MotionControlType::velocity;

  //速度PI环设置
  motor.PID_velocity.P = v_p_1;
  motor.PID_velocity.I = v_i_1;

  //最大电机限制电压
  motor.voltage_limit = 12;   // [V]s

  //速度低通滤波时间常数
  motor.LPF_velocity.Tf = 0.02;

  // angle P controller
  motor.P_angle.P = 20;

  //设置最大速度限制
  motor.velocity_limit = 180; // [rad/s]

  motor.useMonitoring(Serial);

  //初始化电机
  motor.init();

  //初始化 FOC
  motor.initFOC();

  Serial.println(F("Motor ready."));
  Serial.println(F("Set the target velocity using serial terminal:"));


  // 启动闪存文件系统
  if (SPIFFS.begin())
  {
    Serial.println("SPIFFS Started.");
  }
  else
  {
    Serial.println("SPIFFS Failed to Start.");
  }


  Serial.print("System is ready \t Free Heap: ");
  Serial.println(ESP.getFreeHeap());
  Serial.println("-----------------------------------------------");
  Serial.println("");

  Debug_Log_func("setup", 1);
}

char buf[255];
long loop_count = 0;
double last_pitch;
void loop() {
  Debug_Log_func("loop");
  if ( touch_STATE[3] ) {
    ESP32Server.handleClient();
    //delay(1);//allow the cpu to switch to other tasks
    ArduinoOTA.handle();
  }
  motor.loopFOC();

  while (i2cRead(0x3B, i2cData, 14));
  accX = (int16_t)((i2cData[0] << 8) | i2cData[1]);
  accY = (int16_t)((i2cData[2] << 8) | i2cData[3]);
  accZ = (int16_t)((i2cData[4] << 8) | i2cData[5]);
  tempRaw = (int16_t)((i2cData[6] << 8) | i2cData[7]);
  gyroX = (int16_t)((i2cData[8] << 8) | i2cData[9]);
  gyroY = (int16_t)((i2cData[10] << 8) | i2cData[11]);
  gyroZ = (int16_t)((i2cData[12] << 8) | i2cData[13]);

  double dt = (double)(micros() - timer) / 1000000; // Calculate delta time
  timer = micros();

  double pitch = acc2rotation(accX, accY);
  //double pitch2 = atan(-accX / sqrt(accY * accY + accZ * accZ)) * RAD_TO_DEG;
  double gyroZrate = gyroZ / 131.0; // Convert to deg/s
  if (abs(pitch - last_pitch) > 100) {
    //kalmanZ.setAngle(pitch);
  }

  kalAngleZ = kalmanZ.getAngle(pitch, gyroZrate + gyroZ_OFF, dt);
  last_pitch = pitch;
  gyroZangle += (gyroZrate + gyroZ_OFF) * dt;	// Calculate gyro angle without any filter
  compAngleZ = 0.93 * (compAngleZ + (gyroZrate + gyroZ_OFF) * dt) + 0.07 * pitch; // Calculate the angle using a Complimentary filter

  // Reset the gyro angle when it has drifted too much
  if (gyroZangle < -180 || gyroZangle > 180)
    gyroZangle = kalAngleZ;

  pendulum_angle = constrainAngle(fmod(kalAngleZ, 120) - target_angle);	//摆角计算

  //   pendulum_angle当前角度与期望角度差值，在差值大的时候进行摇摆，差值小的时候LQR控制电机保持平衡
  if (test_flag == 0) //正常控制
  {
    if (abs(pendulum_angle) < swing_up_angle) // if angle small enough stabilize 0.5~30°,1.5~90°
    {
      target_velocity = controllerLQR(pendulum_angle, gyroZrate, motor.shaftVelocity());
      if (abs(target_velocity) > motor.velocity_limit)
        target_velocity = _sign(target_velocity) * motor.velocity_limit;

      motor.controller = MotionControlType::velocity;
      motor.move(target_velocity);
    }
    else // else do swing-up
    { // sets swing_up_voltage to the motor in order to swing up
      motor.controller = MotionControlType::torque;
      target_voltage = -_sign(gyroZrate) * swing_up_voltage;
      motor.move(target_voltage);
    }
  }
  else if (test_flag == 1)
  {
    motor.controller = MotionControlType::torque;
    motor.move(target_voltage);
  }
  else
  {
    motor.controller = MotionControlType::velocity;
    motor.move(target_velocity);
  }

  //串口输出数据部分，不需要的情况可以改为0
#if 0

  Serial.print(accX); Serial.print("\t");
  Serial.print(accY); Serial.print("\t");
  Serial.print(atan(accX / accY) / 1.570796 * 90); Serial.print("\t");
  Serial.print(pitch); Serial.print("\t");
  Serial.print(gyroZangle); Serial.print("\t");
  Serial.print(compAngleZ); Serial.print("\t");
  Serial.print(kalAngleZ); Serial.print("\t");

  Serial.print(target_voltage); Serial.print("\t");
  //  Serial.print(target_velocity);Serial.print("\t");
  Serial.print(motor.shaft_velocity); Serial.print("\t");
  Serial.print(target_angle); Serial.print("\t");
  Serial.print(pendulum_angle); Serial.print("\t");
  Serial.print(gyroZrate); Serial.print("\t");
  Serial.print("\r\n");
#endif
  //  motor.move(target_velocity);
  //可以使用该方法wifi发送udp信息
  if (wifi_flag)
  {
    digitalWrite(ACTIVE_PIN, LOW);
    memset(buf, 0, strlen(buf));

    wifi_print("v", motor.shaftVelocity());
    wifi_print("vq", motor.voltage.q);
    wifi_print("p", pendulum_angle);
    wifi_print("t", target_angle);
    wifi_print("k", kalAngleZ);
    wifi_print("g", gyroZrate);
    wifi_print("BAT", driver.voltage_power_supply);

    udp.writeTo((const unsigned char*)buf, strlen(buf), IPAddress(192, 168, 4, 2), localUdpPort); //广播数据
    digitalWrite(ACTIVE_PIN, HIGH);
  }

  //触摸感应处理
  touchAttach(1, T2);
  touchAttach(2, T3);
  touchAttach(3, T4);


  //单击事件处理
  if (touch_touched[1]) {
    //Serial.print("\nLight1 touched ");
    //Serial.println(touch_touched_times[1]);
    touch_touched[1] = false;
  }

  if (touch_touched[2]) {
    //Serial.print("\nLight2 touched ");
    //Serial.println(touch_touched_times[2]);

    touch_touched[2] = false;
  }

  if (touch_touched[3]) {
    //Serial.print("\nLight2 touched ");
    //Serial.println(touch_touched_times[2]);

    touch_touched[3] = false;
  }

  //灯光及按键处理
  if ( touch_STATE[1] ) {
    pride();
    addGlitter(15);
    FastLED.show();
  } else {
    FastLED.clearData();
    FastLED.show();
  }
  
  TenthSecondsSinceStartTask();
}

/* mpu6050加速度转换为角度
            acc2rotation(ax, ay)
            acc2rotation(az, ay) */
double acc2rotation(double x, double y)
{
  double tmp_kalAngleZ = (atan(x / y) / 1.570796 * 90);
  if (y < 0)
  {
    return (tmp_kalAngleZ + 180);
  }
  else if (x < 0)
  {
    //将当前值与前值比较，当前差值大于100则认为异常
    if (!isnan(kalAngleZ) && (tmp_kalAngleZ + 360 - kalAngleZ) > 100) {
      //Serial.print("X<0"); Serial.print("\t");
      //Serial.print(tmp_kalAngleZ); Serial.print("\t");
      //Serial.print(kalAngleZ); Serial.print("\t");
      //Serial.print("\r\n");
      if (tmp_kalAngleZ < 0 && kalAngleZ < 0) //按键右边角
        return tmp_kalAngleZ;
      else  //按键边异常处理
        return tmp_kalAngleZ;
    } else
      return (tmp_kalAngleZ + 360);
  }
  else
  {
    return tmp_kalAngleZ;
  }
}

// function constraining the angle in between -60~60
float constrainAngle(float x)
{
  float a = 0;
  if (x < 0)
  {
    a = 120 + x;
    if (a < abs(x))
      return a;
  }
  return x;
}
// LQR stabilization controller functions
// calculating the voltage that needs to be set to the motor in order to stabilize the pendulum
float controllerLQR(float p_angle, float p_vel, float m_vel)
{
  // if angle controllable
  // calculate the control law
  // LQR controller u = k*x
  //  - k = [40, 7, 0.3]
  //  - k = [13.3, 21, 0.3]
  //  - x = [pendulum angle, pendulum velocity, motor velocity]'

  if (abs(p_angle) > 2.5)	//摆角大于2.5则进入非稳态，记录非稳态时间
  {
    last_unstable_time = millis();
    if (stable)	//如果是稳态进入非稳态则调整为目标角度
    {
      //target_angle = EEPROM.readFloat(0) - p_angle;
      target_angle = EEPROM.readFloat(0);
      stable = 0;
    }
  }
  if ((millis() - last_unstable_time) > 1000 && !stable)	//非稳态进入稳态超过500ms检测，更新目标角为目标角+摆角，假设进入稳态
  {
    //target_angle  -= _sign(target_velocity) * 0.4;
    target_angle = target_angle+p_angle;
    stable = 1;
  }

  if ((millis() - last_stable_time) > 2500 && stable) { //稳态超过2000ms检测，更新目标角
    if (abs(target_velocity) > 3 && abs(target_velocity) < 10) { //稳态速度偏大校正
      last_stable_time = millis();
      target_angle  -= _sign(target_velocity) * 0.2;
    }
  }

  //Serial.println(stable);
  float u;

  if (!stable)	//非稳态计算
  {
    motor.PID_velocity.P = v_p_1;
    motor.PID_velocity.I = v_i_1;
    u = LQR_K3_1 * p_angle + LQR_K3_2 * p_vel + LQR_K3_3 * m_vel;
  }
  else
  {
    motor.PID_velocity.P = v_p_2;
    motor.PID_velocity.I = v_i_2;
    u = LQR_K4_1 * p_angle + LQR_K4_2 * p_vel + LQR_K4_3 * m_vel;
  }

  return u;
}
void wifi_print(char * s, double num)
{
  char str[255];
  char n[255];
  sprintf(n, "%.2f", num);
  strcpy(str, s);
  strcat(str, n);
  strcat(buf + strlen(buf), str);
  strcat(buf, ",\0");
}
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

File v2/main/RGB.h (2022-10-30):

#include <Adafruit_NeoPixel.h>
// Which pin on the Arduino is connected to the NeoPixels?
#define LED_PIN    16
// How many NeoPixels are attached to the Arduino?
#define LED_COUNT 21
unsigned char brightness = 30;
// Declare our NeoPixel strip object:
Adafruit_NeoPixel strip(LED_COUNT, LED_PIN, NEO_GRB + NEO_KHZ800);
// Argument 1 = Number of pixels in NeoPixel strip
// Argument 2 = Arduino pin number (most are valid)
// Argument 3 = Pixel type flags, add together as needed:
//   NEO_KHZ800  800 KHz bitstream (most NeoPixel products w/WS2812 LEDs)
//   NEO_KHZ400  400 KHz (classic 'v1' (not v2) FLORA pixels, WS2811 drivers)
//   NEO_GRB     Pixels are wired for GRB bitstream (most NeoPixel products)
//   NEO_RGB     Pixels are wired for RGB bitstream (v1 FLORA pixels, not v2)
//   NEO_RGBW    Pixels are wired for RGBW bitstream (NeoPixel RGBW products)

unsigned long pixelPrevious = 0;        // Previous Pixel Millis
unsigned long patternPrevious = 0;      // Previous Pattern Millis
int           patternCurrent = 0;       // Current Pattern Number
int           pixelInterval = 50;       // Pixel Interval (ms)
int           pixelQueue = 0;           // Pattern Pixel Queue
int           pixelCycle = 0;           // Pattern Pixel Cycle
uint16_t      pixelCurrent = 0;         // Pattern Current Pixel Number
uint16_t      pixelNumber = LED_COUNT;  // Total Number of Pixels

// Input a value 0 to 255 to get a color value.
// The colours are a transition r - g - b - back to r.
uint32_t Wheel(byte WheelPos) {
  WheelPos = 255 - WheelPos;
  if(WheelPos < 85) {
    return strip.Color(255 - WheelPos * 3, 0, WheelPos * 3);
  }
  if(WheelPos < 170) {
    WheelPos -= 85;
    return strip.Color(0, WheelPos * 3, 255 - WheelPos * 3);
  }
  WheelPos -= 170;
  return strip.Color(WheelPos * 3, 255 - WheelPos * 3, 0);
}
void colorWipe(uint32_t color) {
  strip.setPixelColor(pixelCurrent, color); //  Set pixel's color (in RAM)
  strip.show();                             //  Update strip to match
  pixelCurrent++;                           //  Advance current pixel
  if(pixelCurrent >= pixelNumber)           //  Loop the pattern from the first LED
    pixelCurrent = 0;
}
// Fill the dots one after the other with a color
void colorWipe_delay(uint32_t c, uint8_t wait) {
  for(uint16_t i=0; i<strip.numPixels(); i++) {
    strip.setPixelColor(i, c);
    strip.show();
    delay(wait);
  }
}
void strip1() {
  pixelInterval = 100;   
  int i = 0;
  strip.fill(strip.Color(0, 0, 0));
  for(i;i<5;i++)
  {
      strip.setPixelColor((i+pixelNumber-pixelCycle)%pixelNumber, Wheel((i*10 + pixelQueue) & 255)); 
      strip.setPixelColor((i+pixelNumber-pixelCycle+11)%pixelNumber, Wheel((i*10 + pixelQueue+128) & 255)); 
  }
  strip.show();
  pixelCycle++;
  if(pixelCycle>=pixelNumber)
      pixelCycle = 0;
  pixelQueue++;                             //  Advance current cycle
  if(pixelQueue >= 256)
    pixelQueue = 0;                         //  Loop the cycle back to the begining
    
}
void strip2() {
  int i = 0;
  strip.fill(strip.Color(0, 0, 0));
  for(i;i<5;i++)
  {

      int j =(4-i)%7*(150/5)+1;
      
      strip.setPixelColor((i+pixelNumber-pixelCycle)%pixelNumber, strip.Color(j,j,j)); 
      strip.setPixelColor((i+pixelNumber-pixelCycle+11)%pixelNumber, strip.Color(j,j,j)); 
  }
  strip.show();
  pixelCycle++;
  if(pixelCycle>=pixelNumber)
      pixelCycle = 0;
}
void strip3() {
  int i = 0;
  strip.fill(strip.Color(0, 0, 0));
  for(i;i<5;i++)
  {
      int j =i%7*(150/5)+1;
      strip.setPixelColor((i+pixelCycle)%pixelNumber, strip.Color(j,j,j)); 
      strip.setPixelColor((i+pixelCycle+11)%pixelNumber, strip.Color(j,j,j)); 
  }
  strip.show();
  pixelCycle++;
  if(pixelCycle>=pixelNumber)
      pixelCycle = 0;
}
void rainbow1() {          
  pixelInterval = 30;   
  for(uint16_t i=0; i < pixelNumber; i++) {
    strip.setPixelColor(i, Wheel((i + pixelCycle) & 255)); //  Update delay time  
  }
  strip.show();                             //  Update strip to match
  pixelCycle++;                             //  Advance current cycle
  if(pixelCycle >= 256)
    pixelCycle = 0;                         //  Loop the cycle back to the begining
}
void rainbow2()
{
  pixelInterval = 30;
    pixelCycle +=256; 
    strip.rainbow(pixelCycle);
    strip.show(); // Update strip with new contents
    if(pixelCycle >= 5*65536)
      pixelCycle = 0;
}
void pulse_rainbow1()
{
  pixelInterval = 30;
  pixelQueue+=1;
  if(pixelQueue>=brightness*2)
   pixelQueue = 0;
  if(pixelQueue<brightness)
  strip.setBrightness(pixelQueue); // Set BRIGHTNESS to about 1/5 (max = 255)
  else
  strip.setBrightness(brightness+brightness-pixelQueue); // Set BRIGHTNESS to about 1/5 (max = 255)
  pixelCycle +=256; 
    strip.rainbow(pixelCycle);
    strip.show(); // Update strip with new contents
    if(pixelCycle >= 5*65536)
      pixelCycle = 0;
}
void rgb_off()
{
  pixelInterval = 100;
  strip.fill(strip.Color(0, 0, 0));
  strip.show(); // Update strip with new contents
}
